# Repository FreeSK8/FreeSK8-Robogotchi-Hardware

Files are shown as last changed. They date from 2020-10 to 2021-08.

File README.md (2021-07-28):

# FreeSK8-Robogotchi-Hardware

The [FreeSK8 Robogotchi](https://derelictrobot.com/collections/production/products/freesk8-robogotchi) is an advanced BLE Receiver, Datalogger, and core component of the FreeSK8 System.

Think of it like a blackbox flight recorder for your esk8 or LEV. 

The Robogotchi brings Always-On Logging as a core feature with an asynchronous logging integration with our FreeSK8 Mobile App. 

Ride now, Sync later.

[Robogotchi Documentation @ FreeSK8 Codex](https://codex.freesk8.org/docs/robogotchi)
 
<!-- LICENSE -->
## License

(C) Copyright 2021 - FreeSK8 Foundation NPO

**Licensed under [CERN-OHL-S V2.0](https://ohwr.org/cern_ohl_s_v2.txt)**

https://cern-ohl.web.cern.ch/

<!-- CONTACT -->
## Authors

* Renee Glinski - [@r3n33](https://github.com/r3n33)
* Andrew Dresner - [@DerelictRobot](https://github.com/DerelictRobot)
* Project Link: [https://github.com/FreeSK8](https://github.com/FreeSK8)

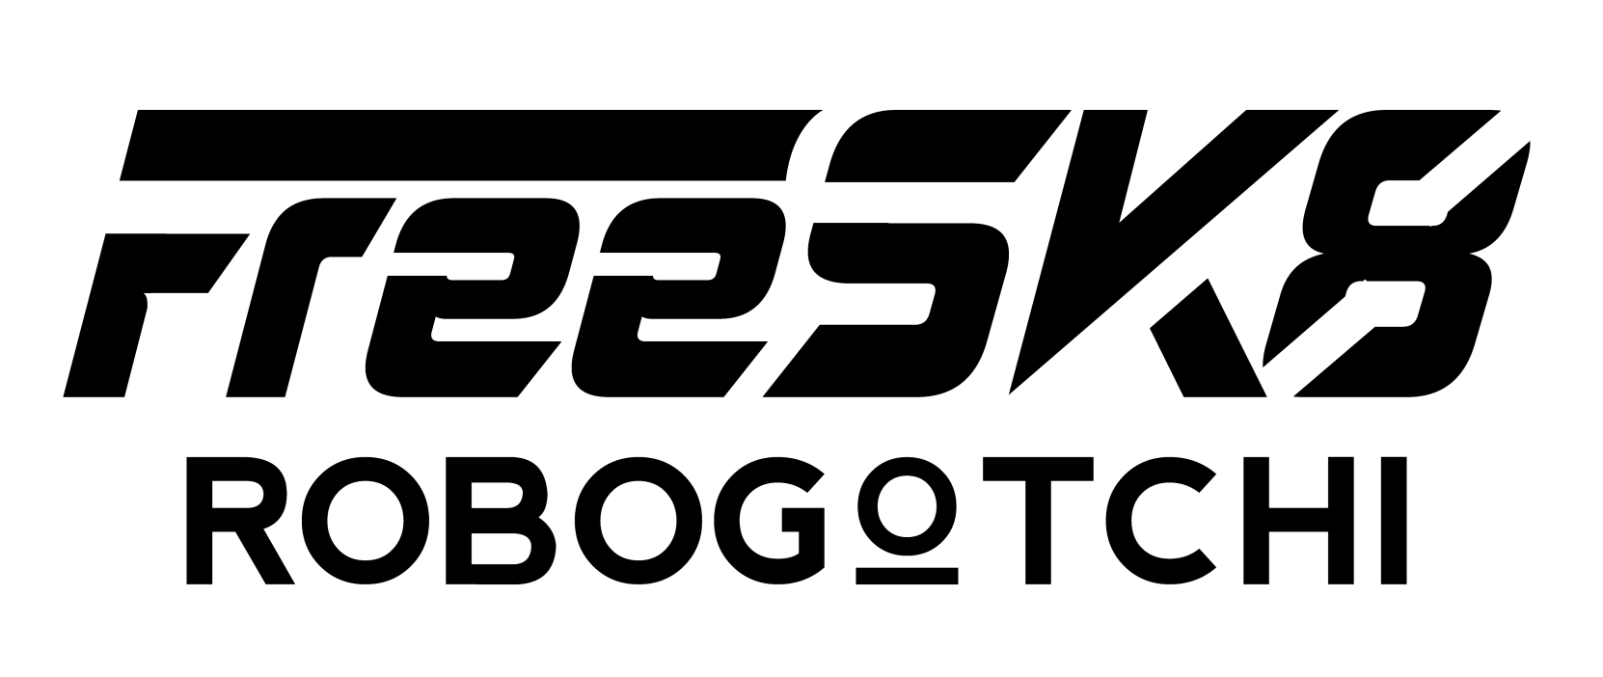
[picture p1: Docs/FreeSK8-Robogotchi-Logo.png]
FreeSK8 Robogotchi


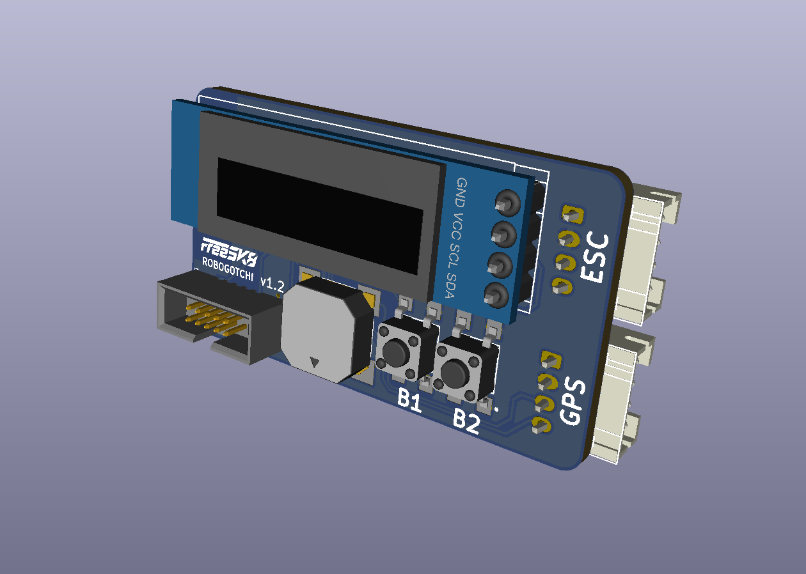
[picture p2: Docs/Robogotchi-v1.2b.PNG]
Robogotchi v1.2


 <!-- CONTRIBUTING -->
## Contributing

Contributions are what make the open source community such an amazing place to be learn, inspire, and create. Any contributions you make are **greatly appreciated**.

1. Fork the Project
2. Create your Feature Branch (`git checkout -b feature/AmazingFeature`)
3. Commit your Changes (`git commit -m 'Add some AmazingFeature'`)
4. Push to the Branch (`git push origin feature/AmazingFeature`)
5. Open a Pull Request

<!-- ACKNOWLEDGEMENTS -->
## Attribution & References

* [VESC-Project](https://vesc-project.com)
* [NRF52 VESC](https://github.com/vedderb/nrf52_vesc)
* [Nordic NRF5 SDK](https://infocenter.nordicsemi.com/index.jsp)

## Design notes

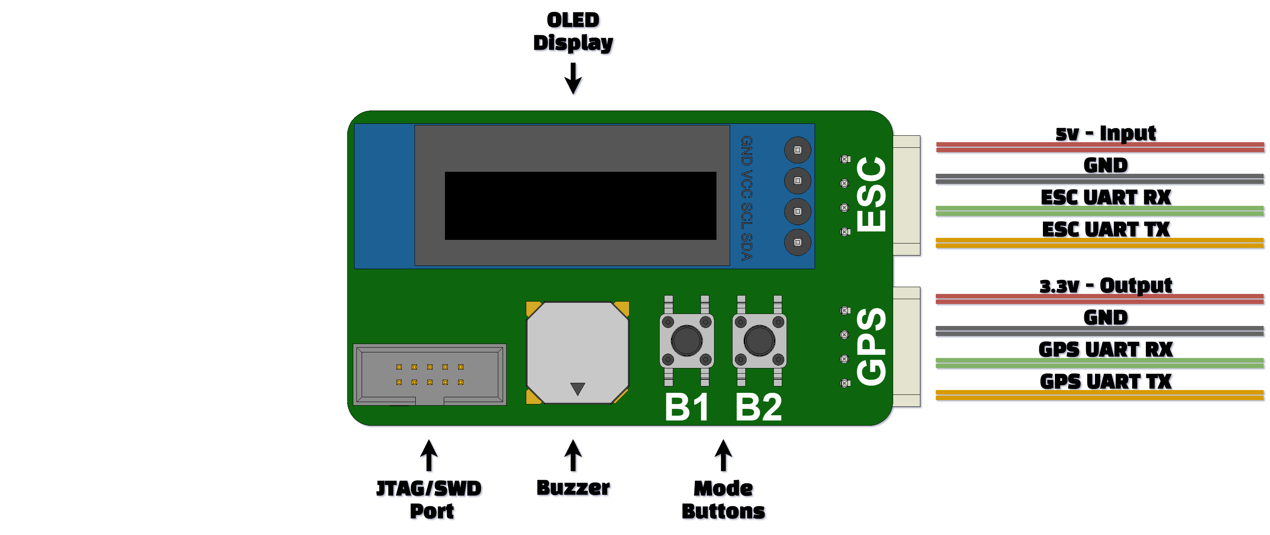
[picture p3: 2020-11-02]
Docs/Robogotchi-pinout.png

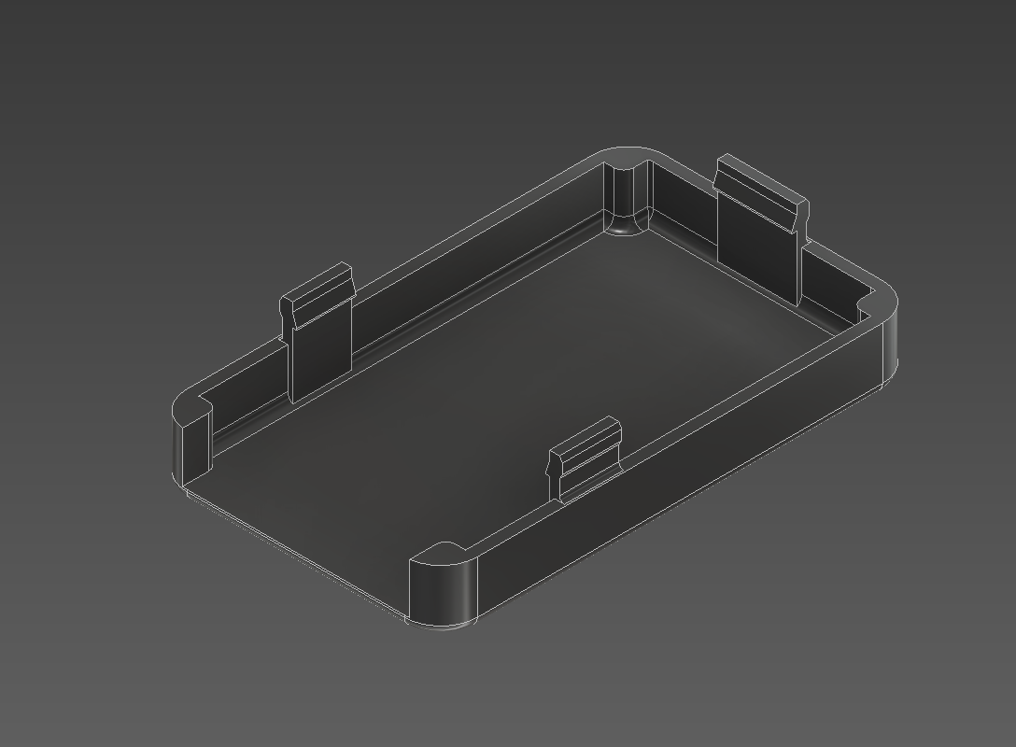
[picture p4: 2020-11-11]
Docs/Robogotchi-Enclosure-Bottom.PNG

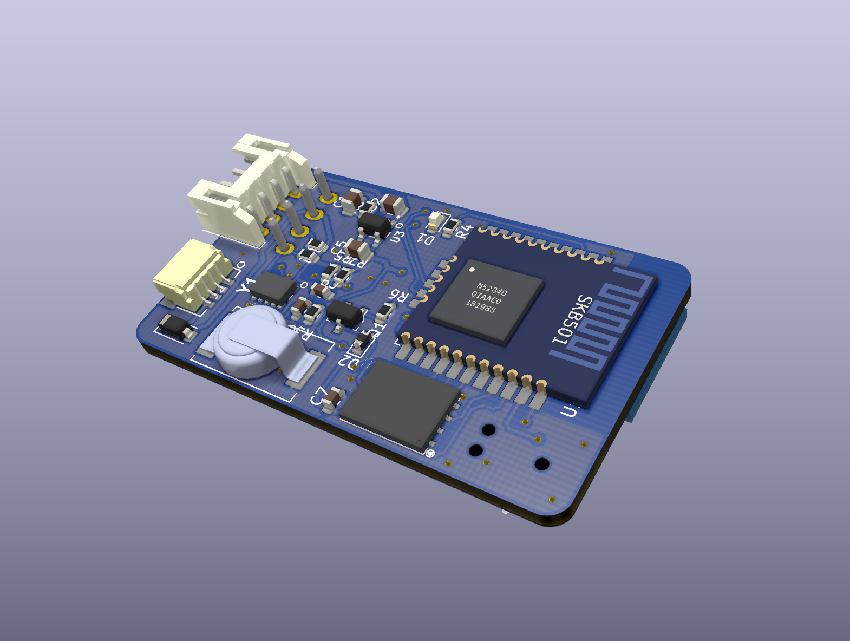
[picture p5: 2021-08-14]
Docs/Robogotchi-v1.5c.PNG

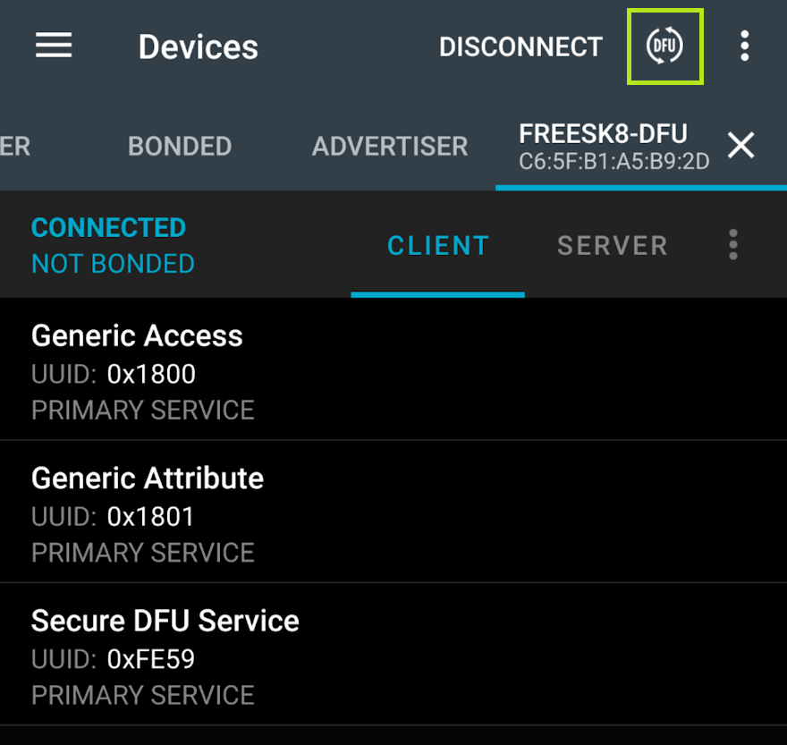
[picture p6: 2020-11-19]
Docs/firmware-update/nrf-connect-dfu.png

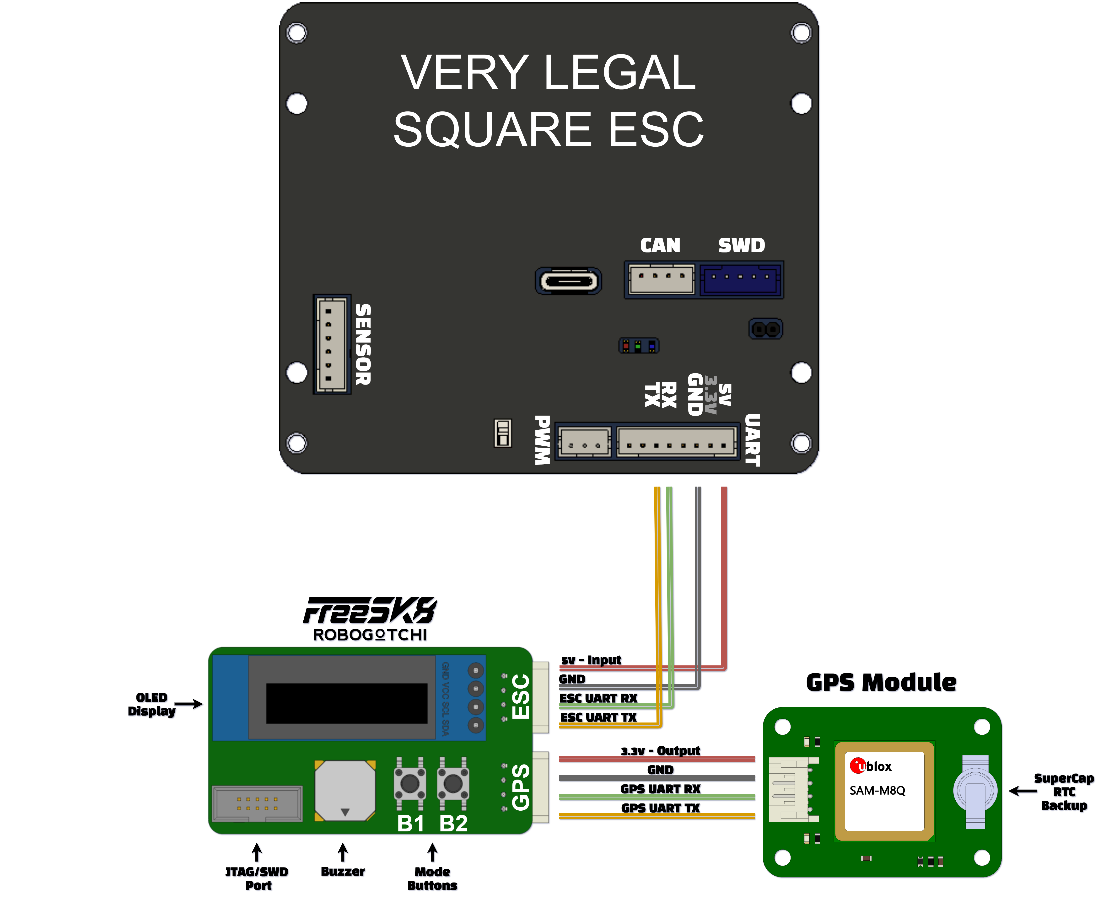
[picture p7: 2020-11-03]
Docs/Robogotchi-GPS-Diagram.png

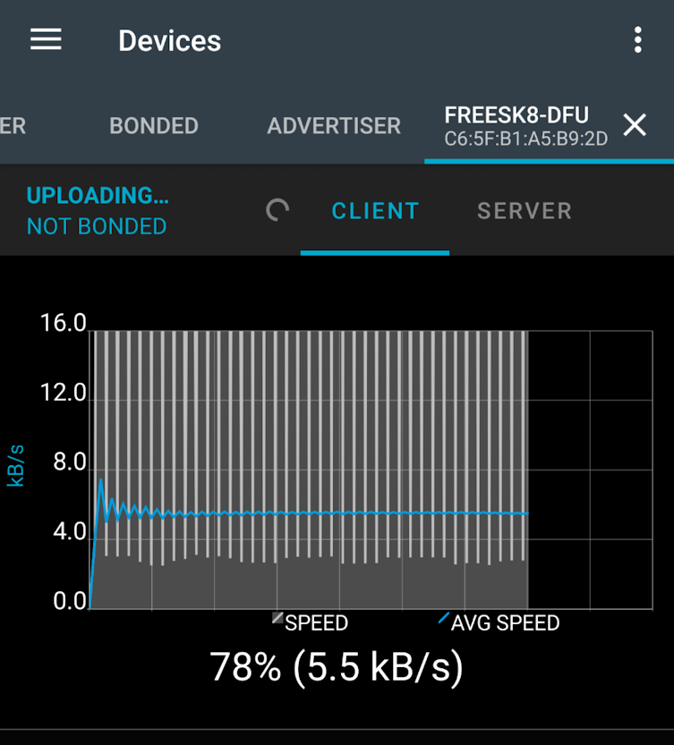
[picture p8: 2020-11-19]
Docs/firmware-update/dfu-transfer.png

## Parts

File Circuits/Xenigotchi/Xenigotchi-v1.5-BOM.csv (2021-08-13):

Comment | Designator | Footprint | LCSC Part #
1.0uF Unpolarized capacitor, small symbol | C1 | C_0603_1608Metric
10uF Unpolarized capacitor, small symbol | C2,C6 | C_0805_2012Metric
DSK-3R3H224U-HL | C3 | CAP_DSK-3R3H224U-HL
0.1uF Unpolarized capacitor, small symbol | C4 | C_0603_1608Metric
10000pF Unpolarized capacitor, small symbol | C5 | C_0603_1608Metric
LED Light emitting diode | D1 | LED_0603_1608Metric
SD0603S040S0R2 Schottky diode | D2 | D_0603_1608Metric
D_Schottky_Small Schottky diode, small symbol | D3 | D_SOD-123
SM04B-SRSS-TB | J1,LCD1,UART2 | SM04B-SRSS-TB
1-1734508-4 | J2 | TE_1-1734508-4
TC2030-CTX | J3 | TAG_TC2030-IDC-NL
CMT-8503-90-SMT-TR | LS1 | XDCR_CMT-8503-90-SMT-TR
2SD1484KT146R | Q1 | SOT-23-3
10k Resistor, small US symbol | R1,R2 | R_0603_1608Metric
470r Resistor, small US symbol | R3 | R_0603_1608Metric
1k Resistor, small US symbol | R4 | R_0603_1608Metric
180r Resistor, small US symbol | R5 | R_0603_1608Metric
20k Resistor, small US symbol | R6 | R_0603_1608Metric
SKB501 | U1 | SKB501_RF_Module
W25N01GVZEIG_TR | U2 | SON127P800X600X80-9N
TLV75533PDBV 500mA Low Dropout Voltage Regulator, Fixed Output 3.3V, SOT-23-5 | U3 | SOT-23-5
RV-3129-C3 | Y1 | ABRTCMC32768kHzEOZ9S3DBT

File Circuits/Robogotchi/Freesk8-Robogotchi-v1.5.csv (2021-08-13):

Comment | Designator | Footprint | LCSC Part #
10uF Unpolarized capacitor, small symbol | C1 | C_0805_2012Metric
1uF Unpolarized capacitor, small symbol | C2,C5 | C_0805_2012Metric
DSK-3R3H224U-HL | C3 | CAP_DSK-3R3H224U-HL
10000pF Unpolarized capacitor, small symbol | C4 | C_0603_1608Metric
0.1uF Unpolarized capacitor, small symbol | C7,C9 | C_0603_1608Metric
LED Light emitting diode | D1 | LED_0603_1608Metric
SD0603S040S0R2 Schottky diode | D2 | D_0603_1608Metric
B130-E3 30V 1A Schottky Barrier Rectifier Diode, SMA(DO-214AC) | D3 | D_SOD-123
S4B-PH-K-SLFSN | J1 | JST_PH_S4B-PH-K_1x04_P2.00mm_Horizontal
SM04B-SRSS-TB | J2 | SM04B-SRSS-TB
TC2030-CTX | J3 | TAG_TC2030-IDC-NL
CMT-8503-90-SMT-TR | LS1 | XDCR_CMT-8503-90-SMT-TR
OLED-0.91 | OLED1 | OLED-0.9
2SD1484KT146R | Q1 | SOT-23-3-R
10k Resistor, small US symbol | R1,R2,R5,R7 | R_0603_1608Metric
470r Resistor, small US symbol | R3 | R_0603_1608Metric
1k Resistor, small US symbol | R4 | R_0603_1608Metric
180r Resistor, small US symbol | R6 | R_0603_1608Metric
20k Resistor, small US symbol | R8 | R_0603_1608Metric
TL3315NF160Q | S1,S2 | SW_TL3305AF260QG
SKB501 | U1 | SKB501_RF_Module
MX25L25645GZ2I-08G | U2 | SON127P800X600X80-9N

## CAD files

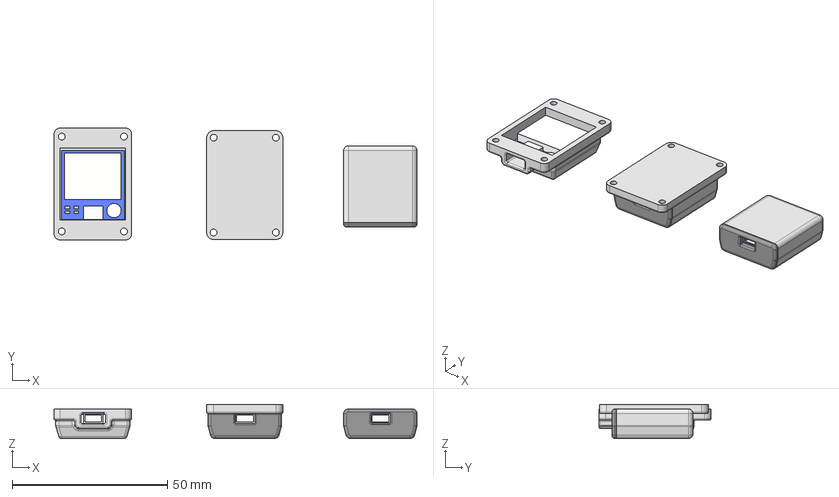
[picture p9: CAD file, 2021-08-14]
3D-Models/GPS-V1.3-ASM.stp
116.8 x 36.0 x 11.0 mm
GPS_Modul_Beitian_BN-220 x 3
GPSv1.3-enclosure
GPSv1.3-enclosure-lid
GPSv1.3-enclosure-4hole
GPSv1.3-enclosure-lid-4hole
GPS-v1.3-Enclosure-ONEPIECE

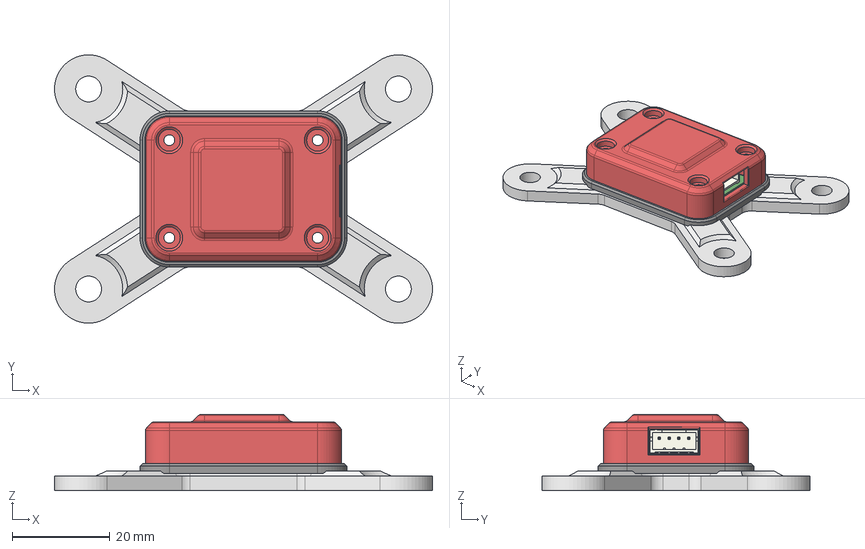
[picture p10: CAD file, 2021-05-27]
3D-Models/GPS-Baseplate-ASM.stp
77.5 x 55.0 x 15.6 mm
GPS-BasePlate-Renee v4
GPS
GPS-Bottom-Enclosure
GPS-Top-Enclosure-v1.2

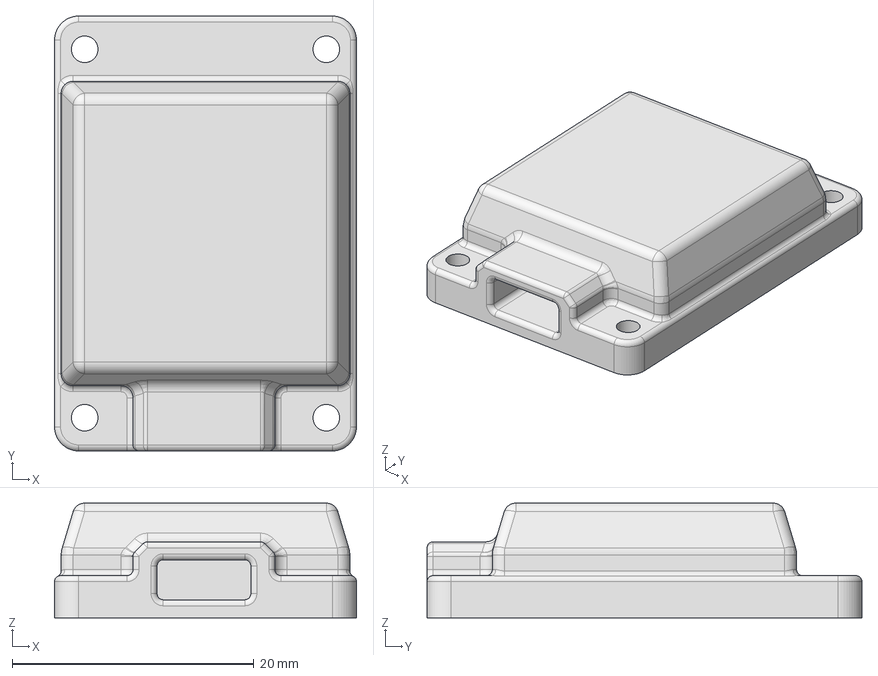
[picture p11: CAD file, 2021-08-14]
3D-Models/GPS-v1.3-Enclosure.step
25.0 x 36.0 x 9.50 mm

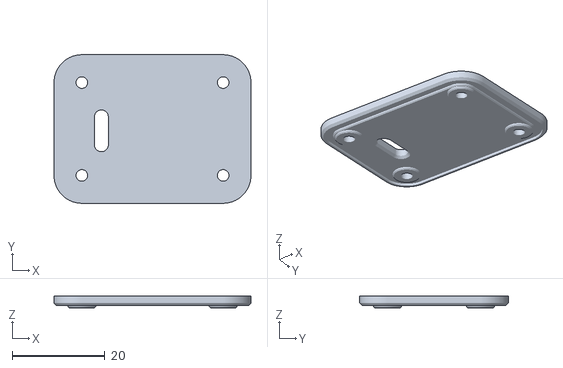
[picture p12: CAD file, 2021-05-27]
3D-Models/GPS-Bottom-Enclosure-v1.2.stl
42.4 x 32.0 x 2.50

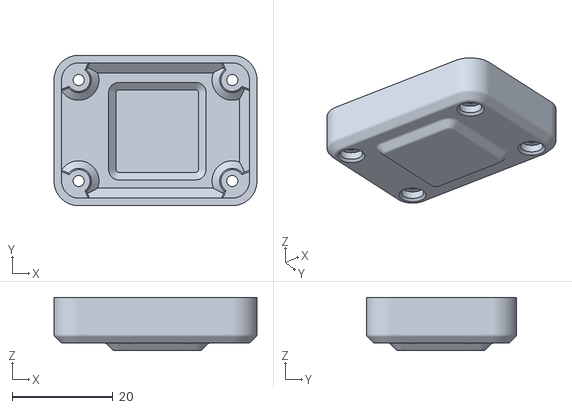
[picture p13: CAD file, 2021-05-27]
3D-Models/GPS-Top-Enclosure-v1.2.stl
40.2 x 29.8 x 10.6

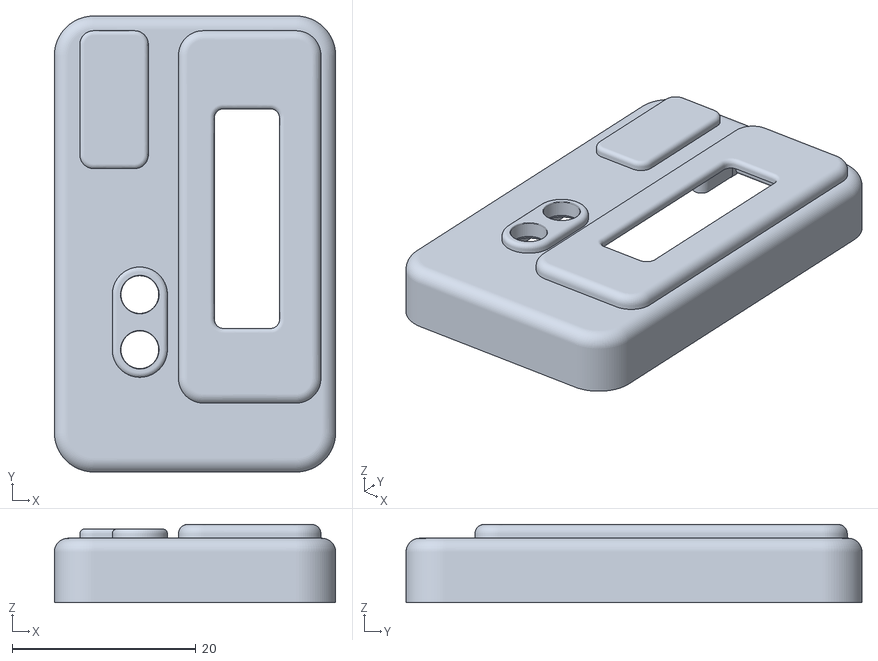
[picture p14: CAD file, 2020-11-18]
3D-Models/Robogotchi-Top-Enclosure-v0.2.stl
30.6 x 49.6 x 8.50

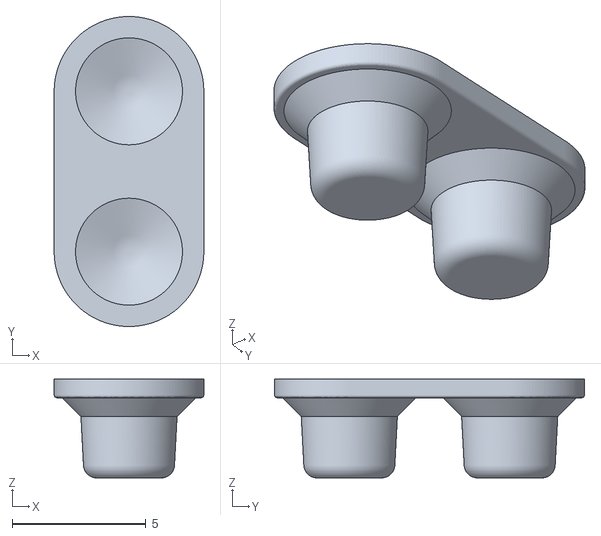
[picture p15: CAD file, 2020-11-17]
3D-Models/Robogotchi-Buttons.stl
5.60 x 11.6 x 3.70

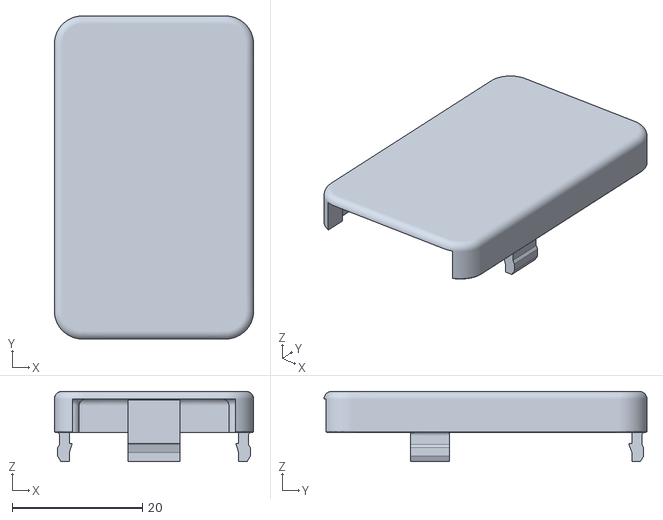
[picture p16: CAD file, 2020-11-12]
3D-Models/Robogotchi-Bottom-Enclosure-v0.2.stl
30.6 x 49.6 x 10.8

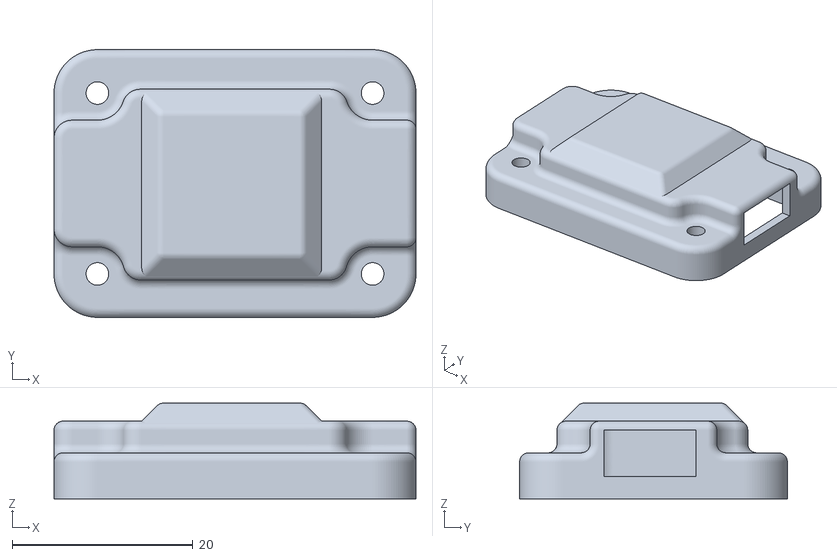
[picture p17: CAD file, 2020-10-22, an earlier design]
3D-Models/GPS-Top-Enclosure.stl
40.0 x 29.6 x 10.6

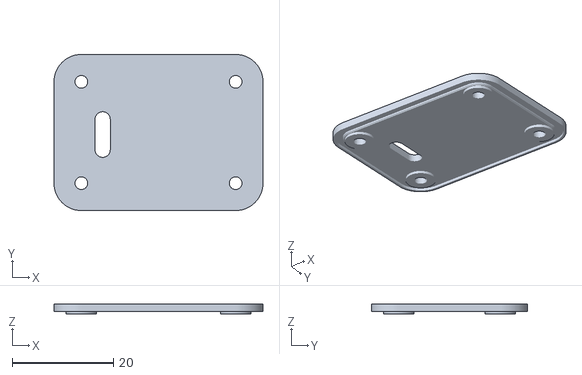
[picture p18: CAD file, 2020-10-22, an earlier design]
3D-Models/GPS-Bottom-Enclosure.stl
41.2 x 30.8 x 2.00

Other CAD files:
3D-Models/GPS-v1.3-Enclosure.stl

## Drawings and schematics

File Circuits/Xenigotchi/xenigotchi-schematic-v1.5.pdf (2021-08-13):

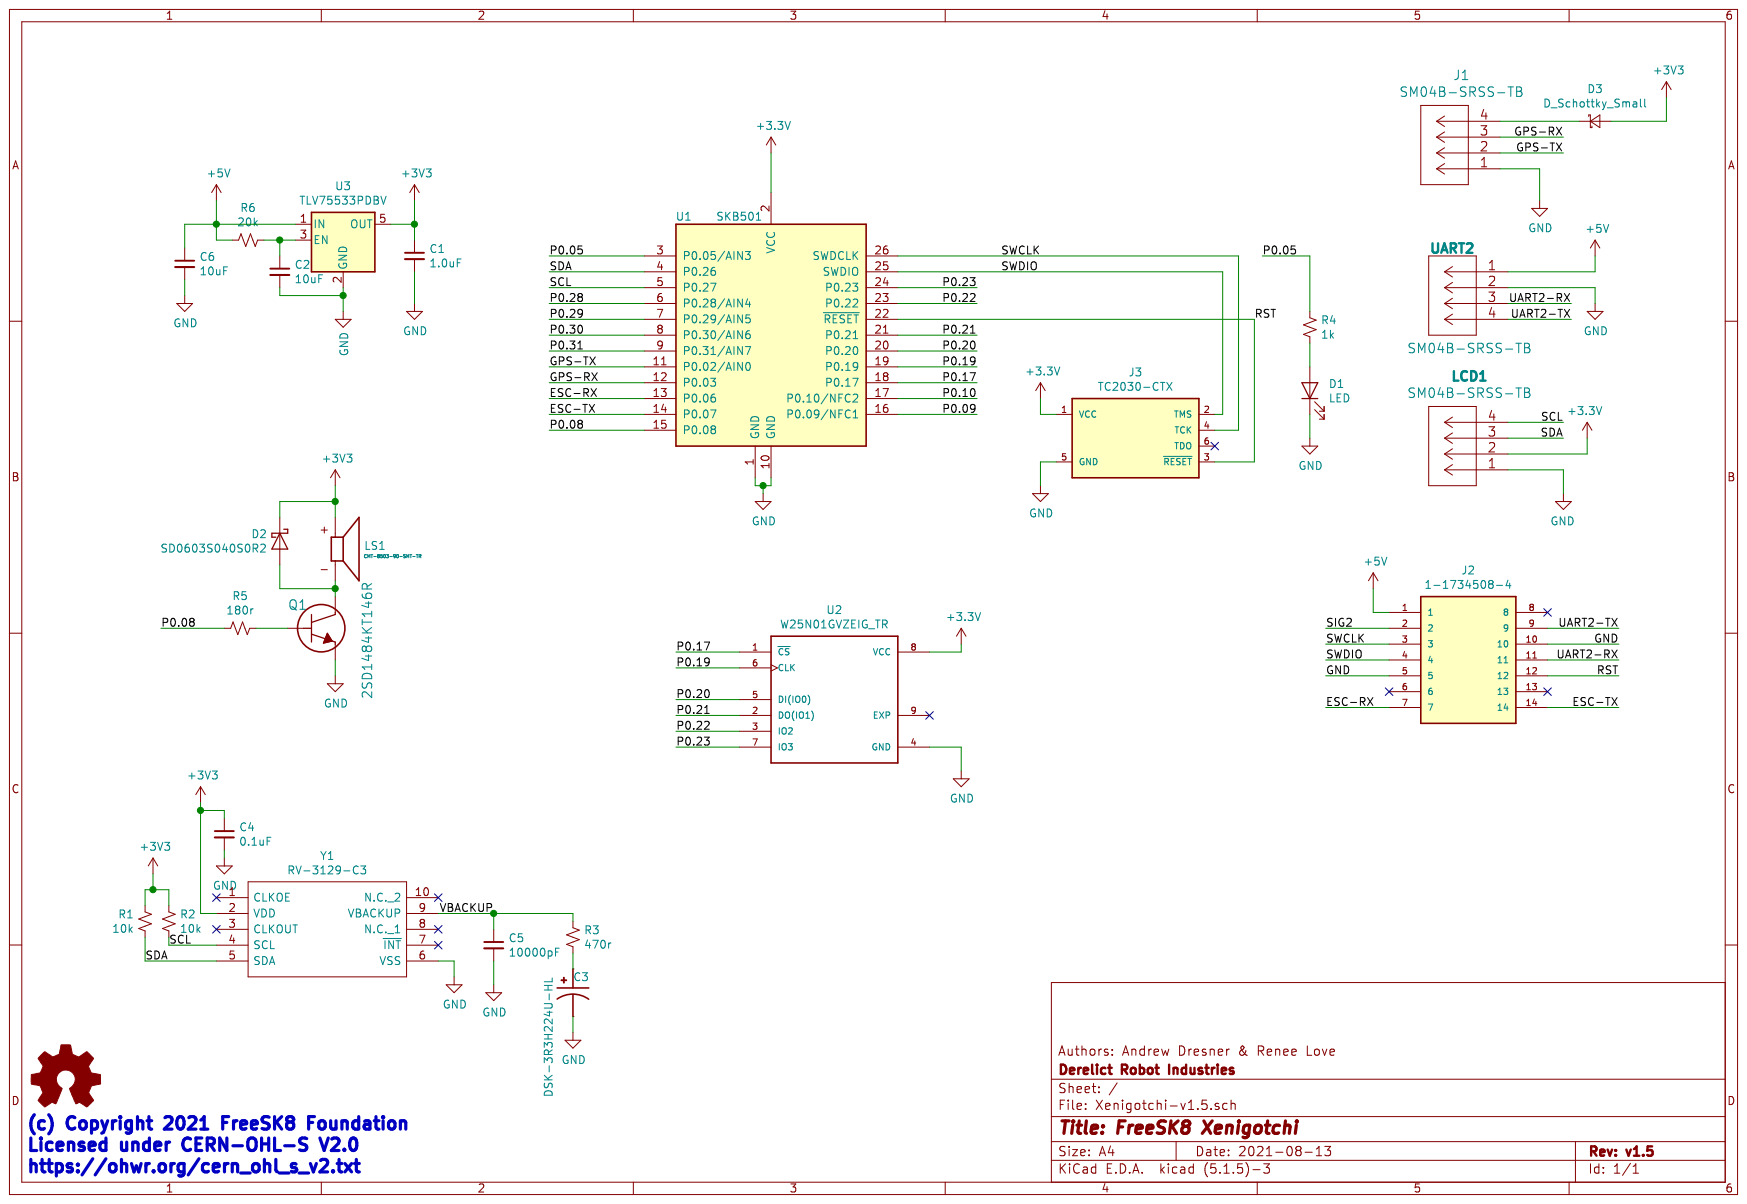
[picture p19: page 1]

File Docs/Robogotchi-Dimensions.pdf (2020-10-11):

1

2

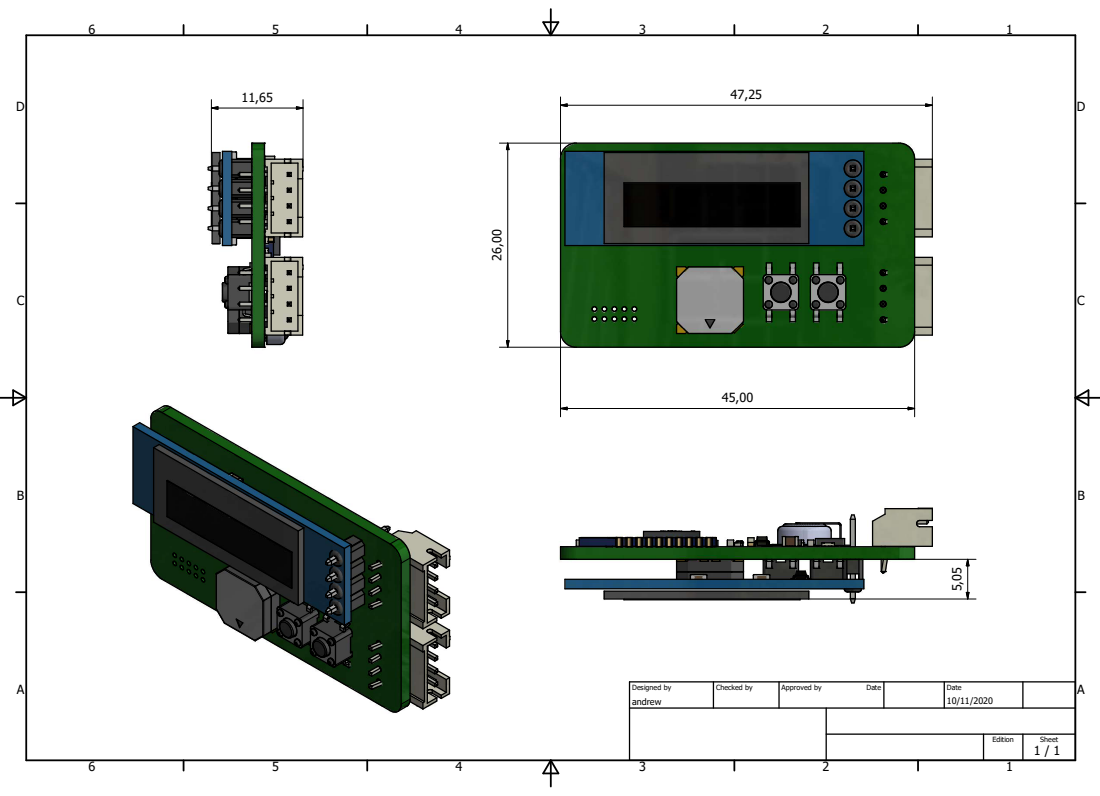
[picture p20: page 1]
andrew; Designed by; Checked by; Approved by; Date; 1 / 1 Edition; Sheet Date

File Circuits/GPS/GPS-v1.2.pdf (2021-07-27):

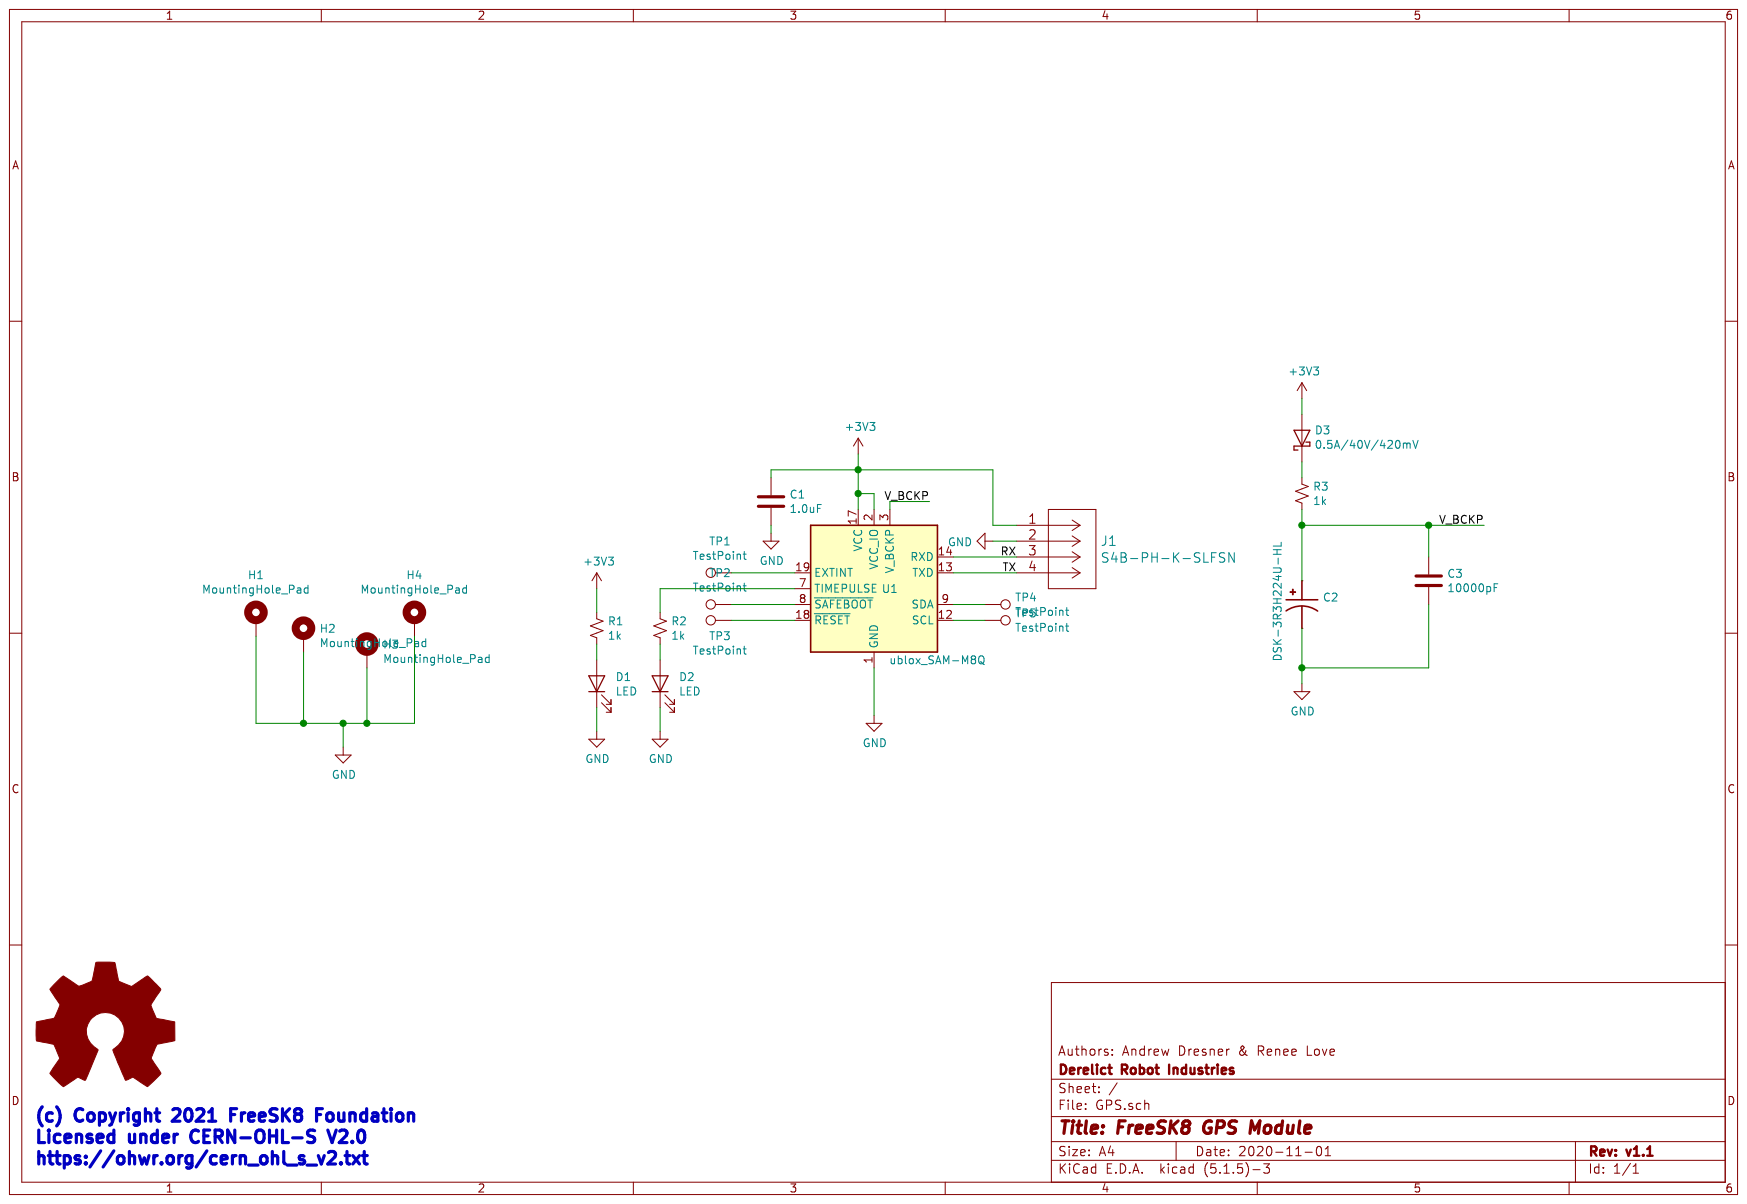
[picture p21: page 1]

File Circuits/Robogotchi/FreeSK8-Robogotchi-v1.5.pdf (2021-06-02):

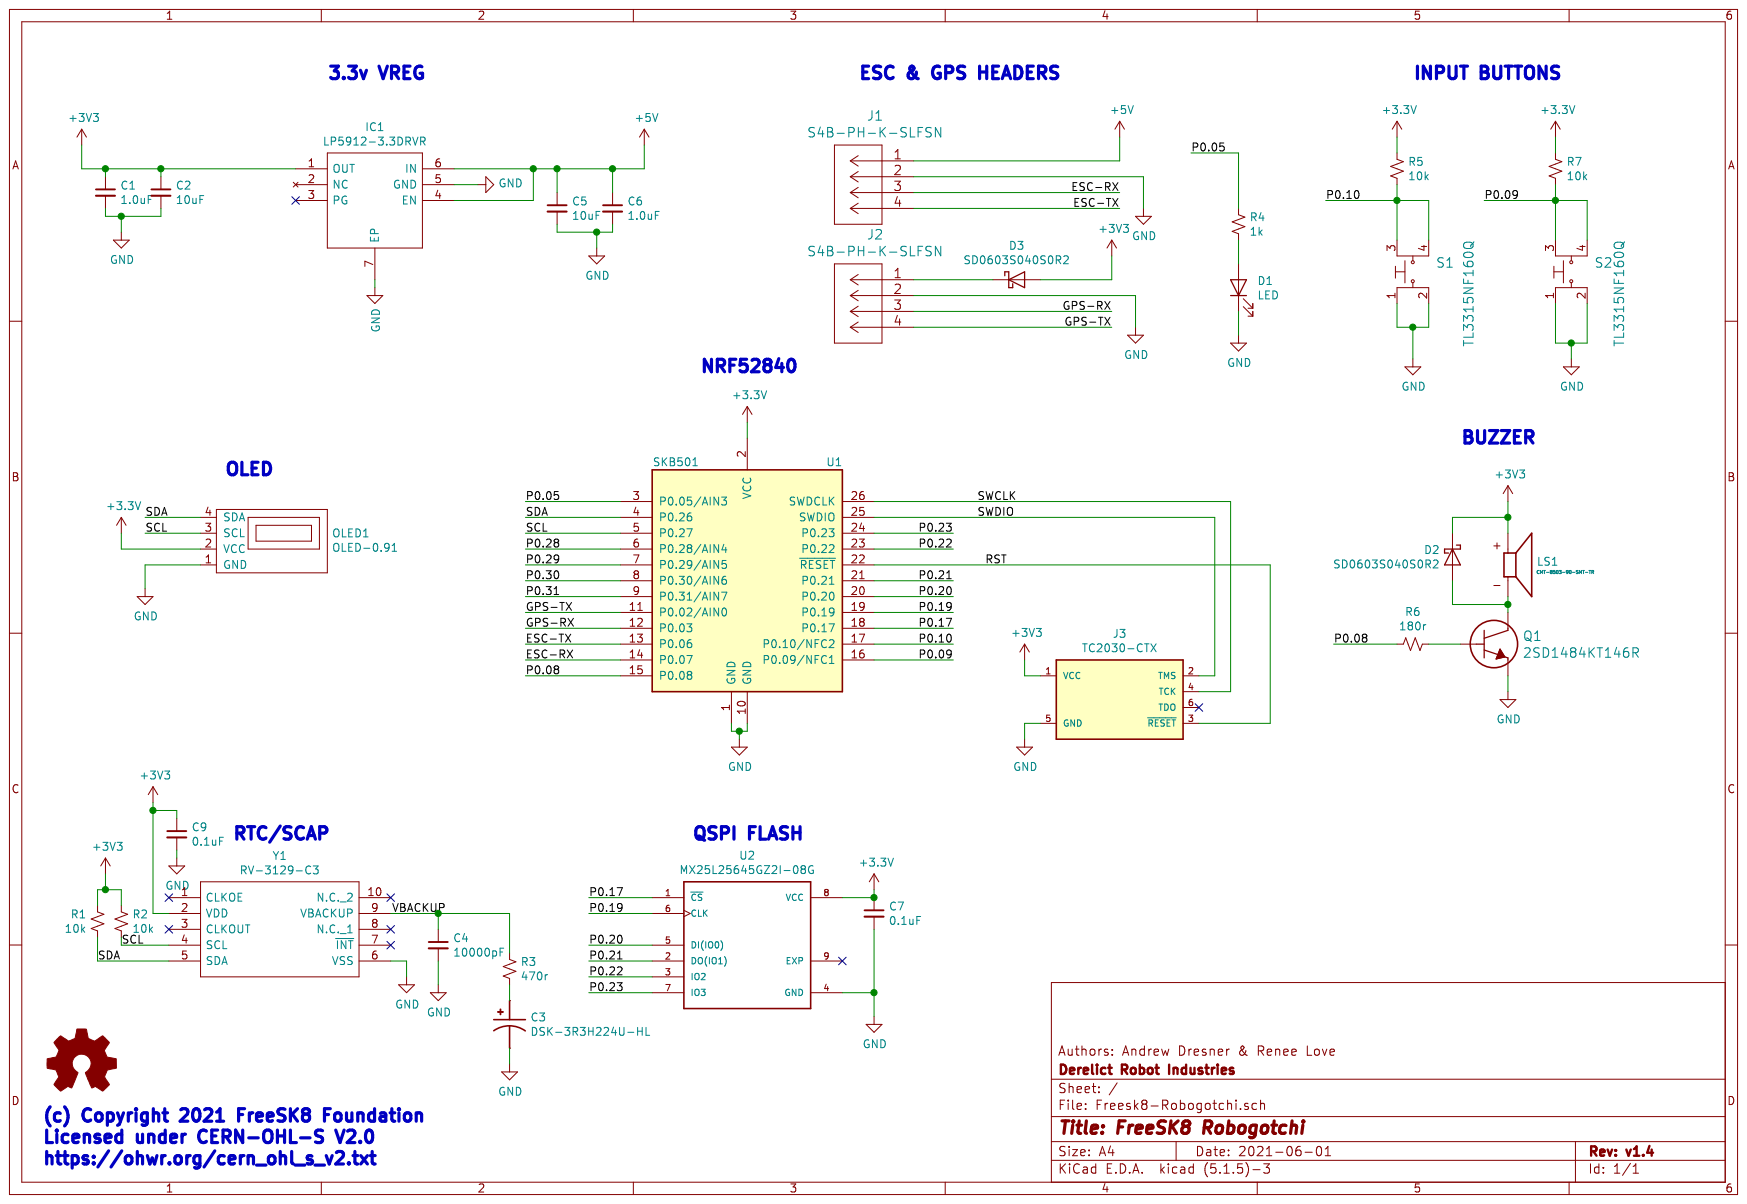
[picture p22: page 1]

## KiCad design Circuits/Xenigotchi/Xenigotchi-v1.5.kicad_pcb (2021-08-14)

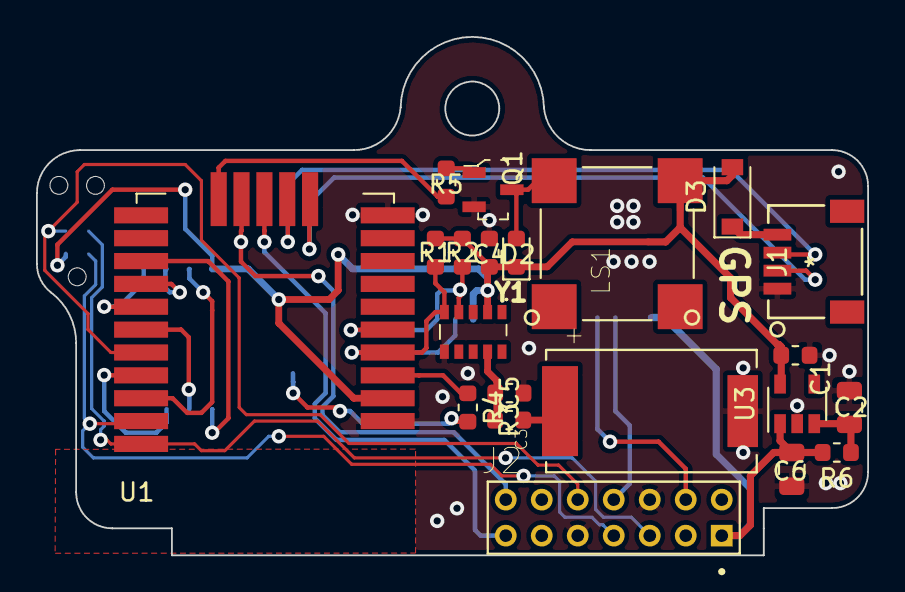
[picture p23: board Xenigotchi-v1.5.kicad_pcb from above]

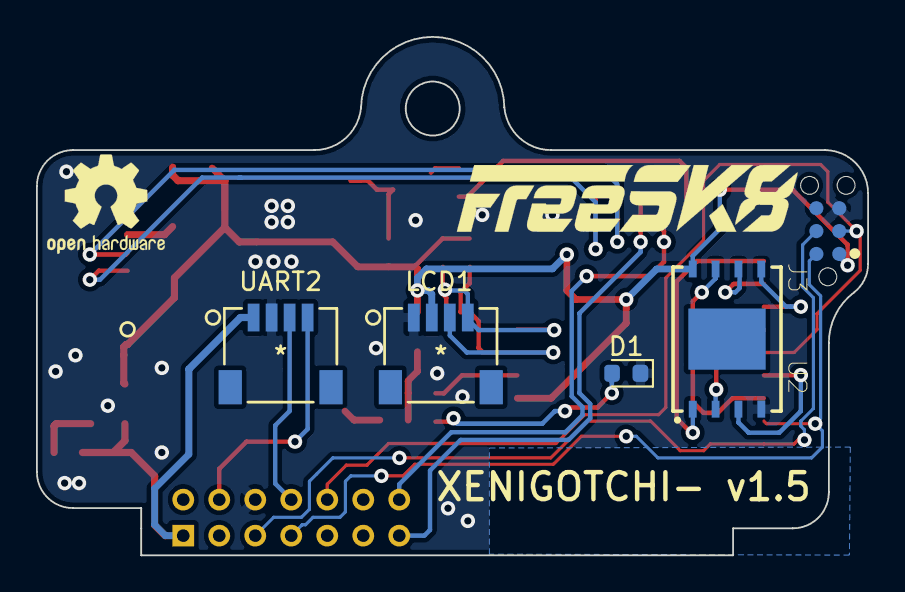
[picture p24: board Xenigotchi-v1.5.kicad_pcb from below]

Board: 2 copper layers, 46.2 x 28.8 mm, 26 parts (5 on the bottom side), 29 nets.

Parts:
C1: 1.0uF; C_0603_1608Metric
C2, C6: 10uF; C_0805_2012Metric
C3: DSK-3R3H224U-HL; CAP_DSK-3R3H224U-HL
C4: 0.1uF; C_0603_1608Metric
C5: 10000pF; C_0603_1608Metric
D1: LED; LED_0603_1608Metric
D2: SD0603S040S0R2; D_0603_1608Metric
D3: D_Schottky_Small; D_SOD-123
J1: SM04B-SRSS-TB
J2: 1-1734508-4; TE_1-1734508-4
J3: TC2030-CTX; TAG_TC2030-IDC-NL
LCD1: SM04B-SRSS-TB
LS1: CMT-8503-90-SMT-TR; XDCR_CMT-8503-90-SMT-TR
Q1: 2SD1484KT146R; SOT-23-3
R1, R2: 10k; R_0603_1608Metric
R3: 470r; R_0603_1608Metric
R4: 1k; R_0603_1608Metric
R5: 180r; R_0603_1608Metric
R6: 20k; R_0603_1608Metric
U1: SKB501; SKB501_RF_Module
U2: W25N01GVZEIG_TR; SON127P800X600X80-9N
U3: TLV75533PDBV; SOT-23-5
UART2: SM04B-SRSS-TB
Y1: RV-3129-C3; ABRTCMC32768kHzEOZ9S3DBT

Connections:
+3V3: C1.1, C4.1, D2.1, D3.2, J3.1, LCD1.2, LS1.P, R1.1, R2.1, U1.2, U2.8, U3.5, Y1.2
+5V: C6.1, J2.1, R6.2, U3.1, UART2.1
/ESC-RX: J2.7, U1.13
/ESC-TX: J2.14, U1.14
/GPS-RX: J1.3, U1.12
/GPS-TX: J1.2, U1.11
/P0.05: R4.1, U1.3
/P0.08: R5.2, U1.15
/P0.17: U1.18, U2.1
/P0.19: U1.19, U2.6
/P0.20: U1.20, U2.5
/P0.21: U1.21, U2.2
/P0.22: U1.23, U2.3
/P0.23: U1.24, U2.7
/RST: J2.12, J3.3, U1.22
/SCL: LCD1.4, R2.2, U1.5, Y1.4
/SDA: LCD1.3, R1.2, U1.4, Y1.5
/SWCLK: J2.3, J3.4, U1.26
/SWDIO: J2.4, J3.2, U1.25
/UART2-RX: J2.11, UART2.3
/UART2-TX: J2.9, UART2.4
/VBACKUP: C5.1, R3.1, Y1.9
GND: C1.2, C2.2, C3.2, C4.2, C5.2, C6.2, D1.1, J1.1, J2.5, J2.10, J3.5, LCD1.1, Q1.1, U1.1, U1.10, U2.4, U3.2, UART2.2, Y1.6
unnamed: C2.1, R6.1, U3.3
unnamed: C3.1, R3.2
unnamed: D1.2, R4.2
unnamed: D2.2, LS1.N, Q1.3
unnamed: D3.1, J1.4
unnamed: Q1.2, R5.1

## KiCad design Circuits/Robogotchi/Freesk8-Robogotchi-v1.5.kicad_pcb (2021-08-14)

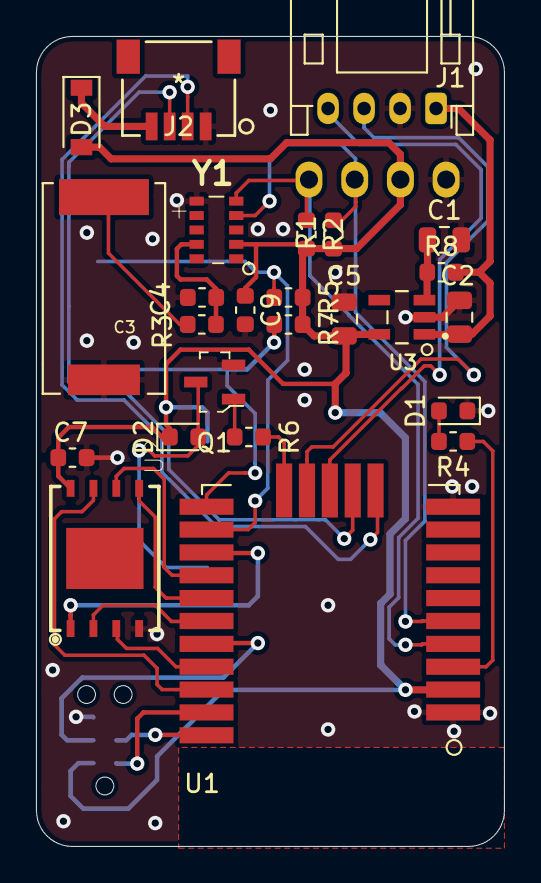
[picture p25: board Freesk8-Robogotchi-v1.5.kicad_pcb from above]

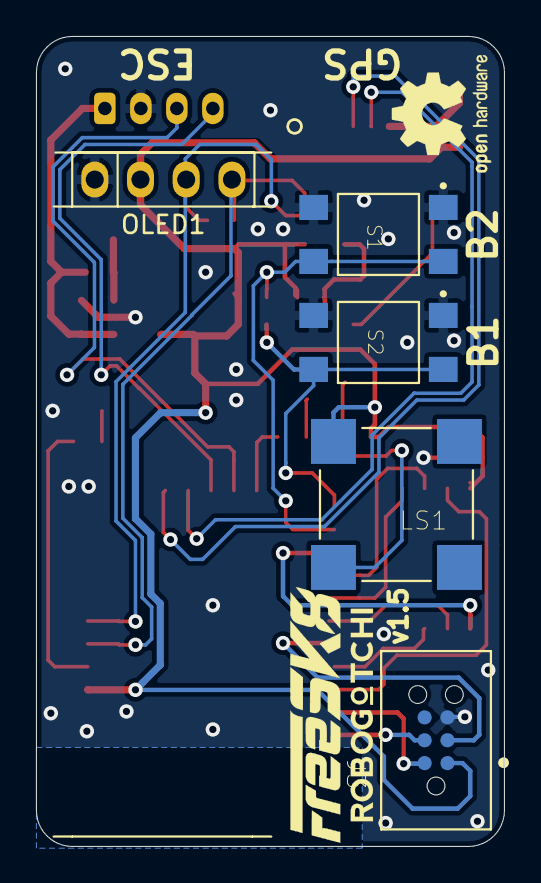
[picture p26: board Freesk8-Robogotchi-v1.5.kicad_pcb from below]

Board: 2 copper layers, 26.0 x 45.0 mm, 30 parts (5 on the bottom side), 29 nets.

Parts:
C1: 10uF; C_0805_2012Metric
C2, C5: 1uF; C_0805_2012Metric
C3: DSK-3R3H224U-HL; CAP_DSK-3R3H224U-HL
C4: 10000pF; C_0603_1608Metric
C7, C9: 0.1uF; C_0603_1608Metric
D1: LED; LED_0603_1608Metric
D2: SD0603S040S0R2; D_0603_1608Metric
D3: B130-E3; D_SOD-123
J1: S4B-PH-K-SLFSN; JST_PH_S4B-PH-K_1x04_P2.00mm_Horizontal
J2: SM04B-SRSS-TB
J3: TC2030-CTX; TAG_TC2030-IDC-NL
LS1: CMT-8503-90-SMT-TR; XDCR_CMT-8503-90-SMT-TR
OLED1: OLED-0.91; OLED-0.9
Q1: 2SD1484KT146R; SOT-23-3-R
R1, R2, R5, R7: 10k; R_0603_1608Metric
R3: 470r; R_0603_1608Metric
R4: 1k; R_0603_1608Metric
R6: 180r; R_0603_1608Metric
R8: 20k; R_0603_1608Metric
S1, S2: TL3315NF160Q; SW_TL3305AF260QG
U1: SKB501; SKB501_RF_Module
U2: MX25L25645GZ2I-08G; SON127P800X600X80-9N
U3: TLV75533PDBVR; SOT95P280X145-5N
Y1: RV-3129-C3; ABRTCMC32768kHzEOZ9S3DBT

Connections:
+3V3: C5.1, C7.1, C9.1, D2.1, D3.2, J3.1, LS1.P, OLED1.2, R1.1, R2.1, R5.1, R7.1, U1.2, U2.8, U3.5, Y1.2
+5V: C2.1, J1.1, R8.2, U3.1
/ESC-RX: J1.3, U1.14
/ESC-TX: J1.4, U1.13
/GPS-RX: J2.3, U1.12
/GPS-TX: J2.2, U1.11
/P0.05: R4.1, U1.3
/P0.08: R6.2, U1.15
/P0.09: R7.2, S2.3, S2.4, U1.16
/P0.10: R5.2, S1.3, S1.4, U1.17
/P0.17: U1.18, U2.1
/P0.19: U1.19, U2.6
/P0.20: U1.20, U2.5
/P0.21: U1.21, U2.2
/P0.22: U1.23, U2.3
/P0.23: U1.24, U2.7
/RST: J3.3, U1.22
/SCL: OLED1.3, R2.2, U1.5, Y1.4
/SDA: OLED1.4, R1.2, U1.4, Y1.5
/SWCLK: J3.4, U1.26
/SWDIO: J3.2, U1.25
/VBACKUP: C4.1, R3.1, Y1.9
GND: C1.2, C2.2, C3.2, C4.2, C5.2, C7.2, C9.2, D1.1, J1.2, J2.1, J3.5, OLED1.1, Q1.1, S1.1, S1.2, S2.1, S2.2, U1.1, U1.10, U2.4, U3.2, Y1.6
unnamed: C1.1, R8.1, U3.3
unnamed: C3.1, R3.2
unnamed: D1.2, R4.2
unnamed: D2.2, LS1.N, Q1.3
unnamed: D3.1, J2.4
unnamed: Q1.2, R6.1

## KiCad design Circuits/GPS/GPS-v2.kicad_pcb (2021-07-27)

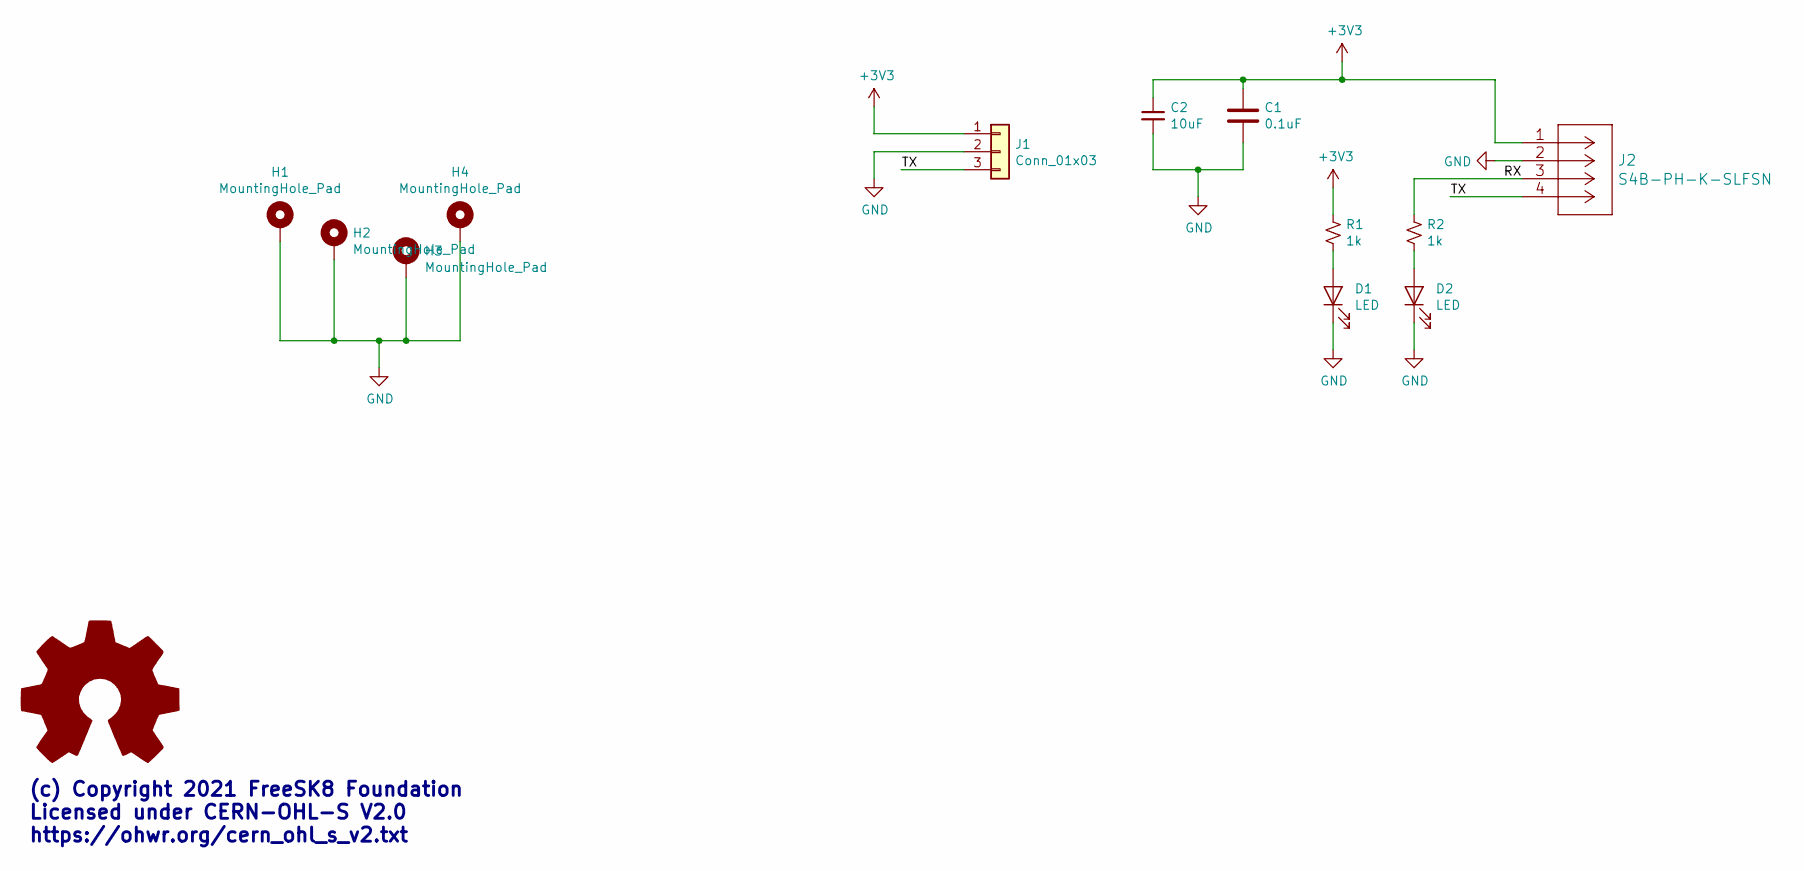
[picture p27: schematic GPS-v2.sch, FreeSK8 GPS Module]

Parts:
C1: 0.1uF; C_0603_1608Metric
C2: 10uF; C_0805_2012Metric
D1, D2: LED; LED_0603_1608Metric
H1, H2, H3, H4: MountingHole_Pad; MountingHole_2.5mm_Pad
J1: Conn_01x03; JST_SH_SM03B-SRSS-TB_1x03-1MP_P1.00mm_Horizontal
J2: S4B-PH-K-SLFSN; JST_PH_S4B-PH-K_1x04_P2.00mm_Horizontal
R1, R2: 1k; R_0603_1608Metric

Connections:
+3V3: C1.1, C2.1, J1.1, J2.1, R1.1
/RX: J2.3, R2.1
/TX: J1.3, J2.4
GND: C1.2, C2.2, D1.1 (K), D2.1 (K), H1.1, H2.1, H3.1, H4.1, J1.2, J2.2
unnamed: D1.2 (A), R1.2
unnamed: D2.2 (A), R2.2

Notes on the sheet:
(c) Copyright 2021 FreeSK8 Foundation Licensed under CERN-OHL-S V2.0 https://ohwr.org/cern_ohl_s_v2.txt

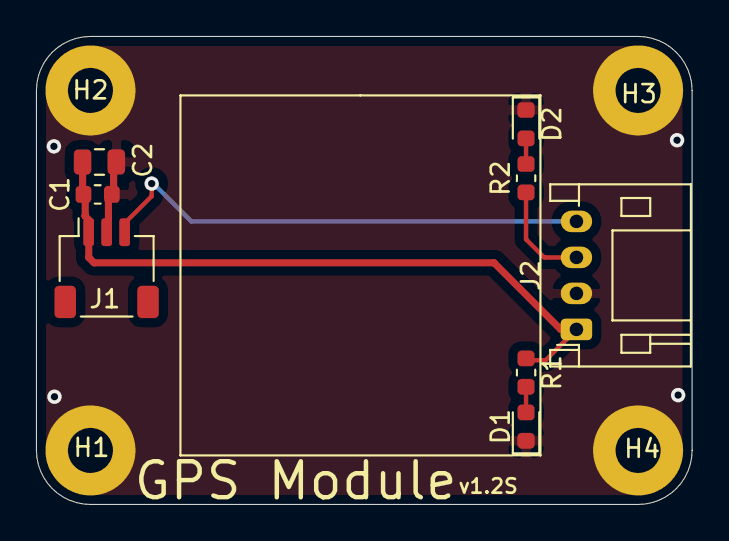
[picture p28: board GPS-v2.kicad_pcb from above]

Board: 2 copper layers, 36.4 x 26.0 mm, 12 parts (0 on the bottom side), 6 nets.

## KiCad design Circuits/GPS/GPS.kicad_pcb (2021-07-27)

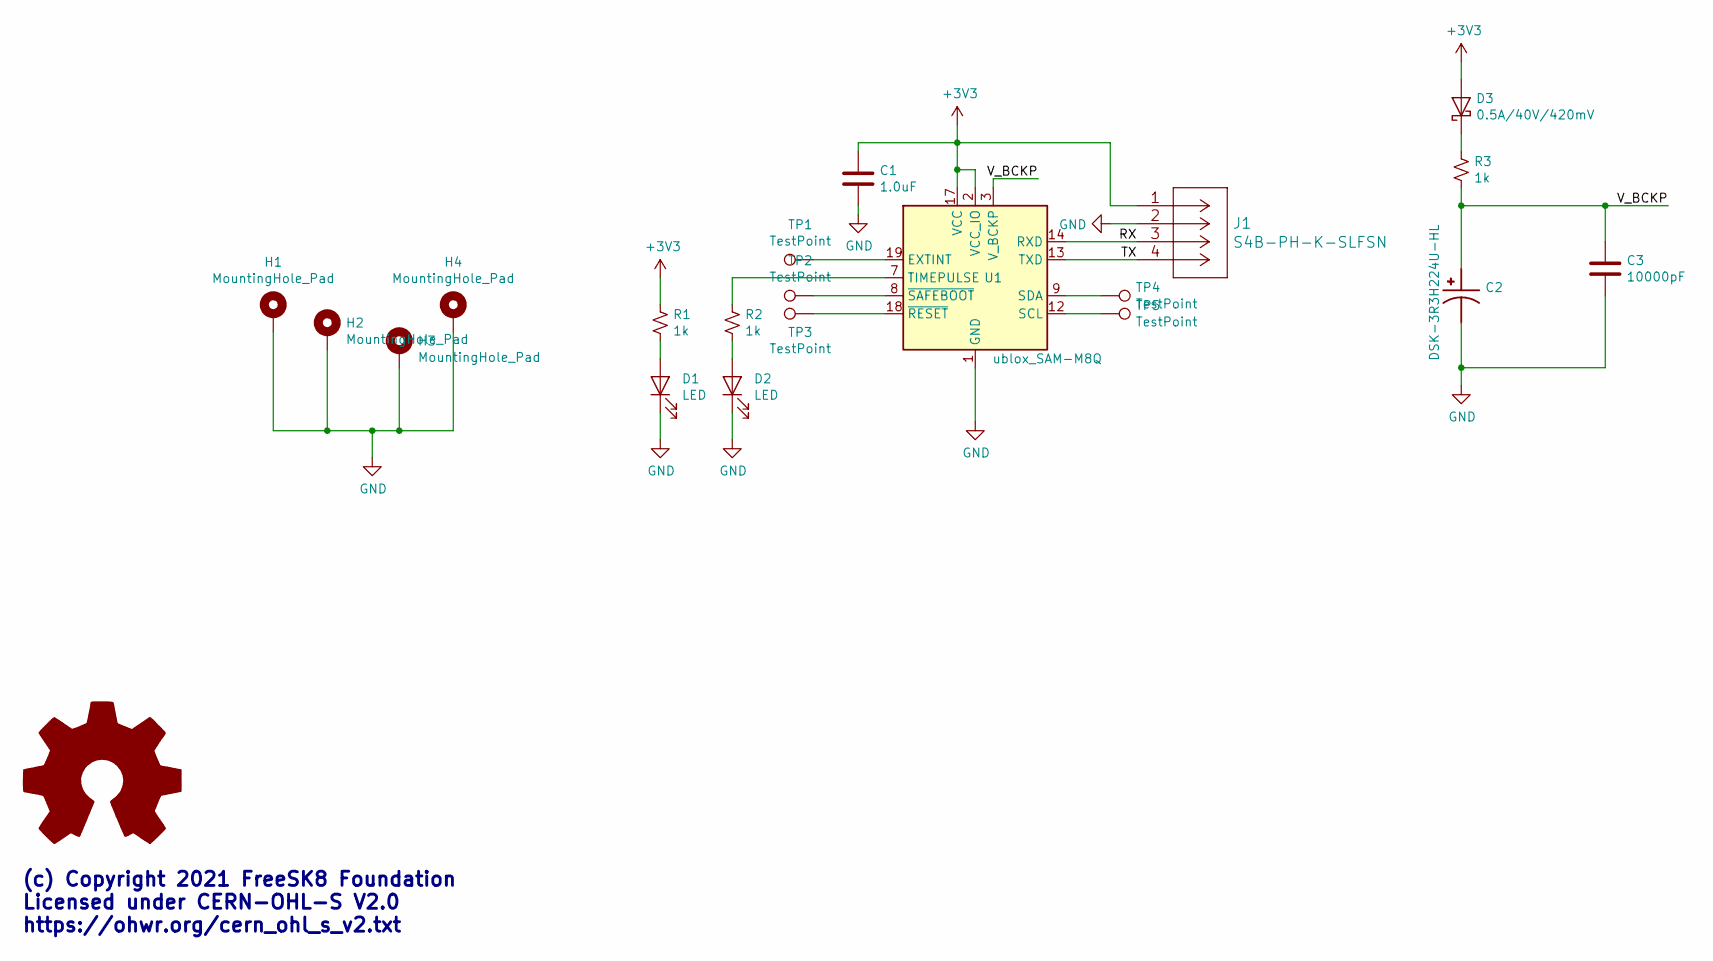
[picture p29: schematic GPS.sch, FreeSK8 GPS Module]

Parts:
C1: 1.0uF; C_0603_1608Metric
C2: DSK-3R3H224U-HL; CAP_DSK-3R3H224U-HL
C3: 10000pF; C_0603_1608Metric
D1, D2: LED; LED_0603_1608Metric
D3: 0.5A/40V/420mV; D_0603_1608Metric
H1, H2, H3, H4: MountingHole_Pad; MountingHole_2.5mm_Pad
J1: S4B-PH-K-SLFSN; JST_PH_S4B-PH-K_1x04_P2.00mm_Horizontal
R1, R2, R3: 1k; R_0603_1608Metric
TP1, TP2, TP3, TP4, TP5: TestPoint; TestPoint_Pad_1.0x1.0mm
U1: ublox_SAM-M8Q; ublox_SAM-M8Q_HandSolder

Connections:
+3V3: C1.1, D3.2 (A), J1.1, R1.1, U1.2 (VCC_IO), U1.17 (VCC)
/RX: J1.3, U1.14 (RXD)
/TX: J1.4, U1.13 (TXD)
/V_BCKP: C2.1, C3.1, R3.2, U1.3 (V_BCKP)
GND: C1.2, C2.2, C3.2, D1.1 (K), D2.1 (K), H1.1, H2.1, H3.1, H4.1, J1.2, U1.1 (GND), U1.4 (GND), U1.5 (GND), U1.6 (GND), U1.10 (GND), U1.11 (GND), U1.15 (GND), U1.16 (GND), U1.20 (GND)
unnamed: D1.2 (A), R1.2
unnamed: D2.2 (A), R2.2
unnamed: D3.1 (K), R3.1
unnamed: R2.1, U1.7 (TIMEPULSE)
unnamed: TP1.1, U1.19 (EXTINT)
unnamed: TP2.1, U1.8 (~SAFEBOOT)
unnamed: TP3.1, U1.18 (~RESET)
unnamed: TP4.1, U1.9 (SDA)
unnamed: TP5.1, U1.12 (SCL)

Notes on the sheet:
(c) Copyright 2021 FreeSK8 Foundation Licensed under CERN-OHL-S V2.0 https://ohwr.org/cern_ohl_s_v2.txt

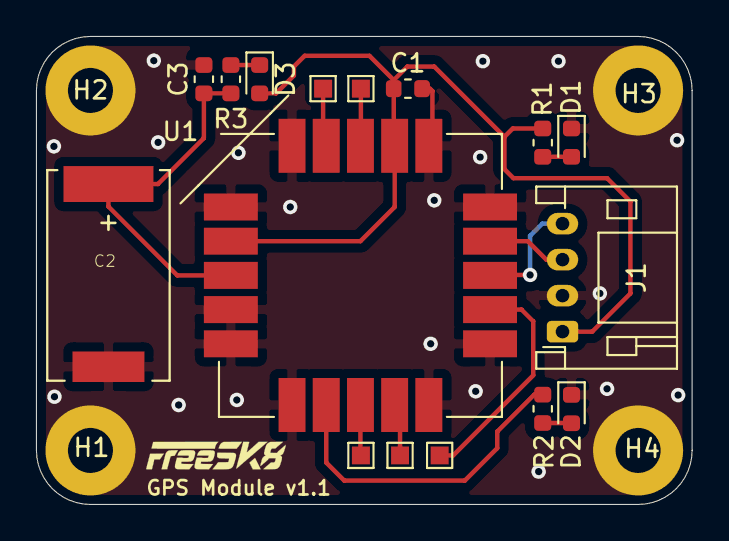
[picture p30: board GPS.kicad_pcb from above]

Board: 2 copper layers, 36.4 x 26.0 mm, 20 parts (0 on the bottom side), 14 nets.

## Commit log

2020-10-22 GPS Module & Enclosure models
    [GPS-Baseplate-ASM.stp, GPS-Bottom-Enclosure.stl, GPS-Top-Enclosure.stl]
2020-11-02 Added Schematics + dimensional drawings.
2020-11-03 GPS Module schematic & docs
2020-11-07 Reorg docs & models
    [GPS-Baseplate-ASM.stp, GPS-Bottom-Enclosure.stl, GPS-Top-Enclosure.stl]
2020-11-11 Robogotchi Enclosure upload/first commit
    3 pieces, top & bottom shell + buttons
    [Robogotchi-Bottom-Enclosure-vBETA.stl, Robogotchi-Bottom-Enclosure-vBETA.stp, Robogotchi-Buttons.stl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]
2020-11-11 Added Robogotchi Enclosure images
2020-11-12 rev0.2 updates to enclosure, file cleanup
    [Robogotchi-Bottom-Enclosure-v0.2.stl, Robogotchi-Bottom-Enclosure-vBETA.stl, Robogotchi-Bottom-Enclosure-vBETA.stp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]
2020-11-12 Adjusted top-enclosure OLED window
    [Robogotchi-Top-Enclosure-v0.2.stl]
2020-11-17 Minor button/hole clearance updates
    [Robogotchi-Buttons.stl, Robogotchi-Top-Enclosure-v0.2.stl]
2020-11-18 Minor changes to internal features for print quality
    [Robogotchi-Top-Enclosure-v0.2.stl]
2021-05-15 Rename Schematics folder to Circuits
2021-05-27 Updated GPS Enclosure STL + ASM of entire assembly
    [GPS-Baseplate-ASM.stp, GPS-Bottom-Enclosure-v1.2.stl, GPS-Top-Enclosure-v1.2.stl]
2021-06-02 v1.4 Robogotchi Schematic update
2021-07-27 Robogotchi KiCAD Design source, initial upload.
    Here we gooooo!
    [Freesk8-Robogotchi-v1.4-BOM.csv, Freesk8-Robogotchi-v1.4.kicad_pcb, Freesk8-Robogotchi-v1.4.sch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]
2021-07-27 added GPS schematic
2021-07-27 Xenigotchi v1.3 schematic PDF
2021-08-13 Robogotchi & Xenigotchi v1.5 updates
    Added gerbers + changed GPS headers to JST SM 1.0mm pitch connectors.
    [Freesk8-Robogotchi-v1.4-BOM.csv, Freesk8-Robogotchi-v1.4.kicad_pcb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]
2021-08-14 Docs/renders upload
    [Freesk8-Robogotchi-v1.5.kicad_pcb, Xenigotchi-v1.5.kicad_pcb]
2021-08-14 Add GPS v1.3 enclosure
    Using BN-220 GPS module for v1.3 for simplicity & cost savings.
    [GPS-V1.3-ASM.stp, GPS-v1.3-Enclosure.step, GPS-v1.3-Enclosure.stl]

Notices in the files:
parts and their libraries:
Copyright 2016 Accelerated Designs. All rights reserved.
